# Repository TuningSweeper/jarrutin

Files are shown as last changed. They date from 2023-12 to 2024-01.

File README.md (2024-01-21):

# jarrutin
 Sähköinen jarrutinprojekti
 
 Tästä himmelistä tulee isona sähköinen jarru erääseen muutoin vähemmän sähköiseen järjestelmään.

## Toimintalogiikasta

Jarrutus viimekädessä toimii oikosulkemalla kestomagneettimoottoria.

Moottori on kytketty kolmivaiheiseen diodisiltaan, minkä tarvittaessa oikosulkee n-fetti. Jännitteet ja virrat saattavat olla aika kovia. Sen takia fettiä ajetaan erillisellä ajurilla, mikä pitää huolen siitä, että tilanmuutokset ovat riittävän nopeita. Viimeisimmässä protossa fettejä on neljä rinnan, ettei paketti kuumene liikaa. Seuraavaa iteraatioon pitäisi vähän parantaa diodisillan ja fettien jäähdytystä. Siinä ehjä kannattaa unohtaa piirilevyt ja laittaa reilut rivat, ja niihin komponentit kiinni.

Nopeusanturina on moottorin oma hall-anturi. Sille annetaan 5v ja sieltä tulee avokollektorilähdön kautta nopeustieto. 4N35 -optoerottimella saadaan tehtyä optinen erotus ja samalla jännitteenmuunnos 3.3 V logiikalle. On vähän epäselvää mikä se hall-anturi on, ja toimisiko se kolmella voltilla. Jokatapauksessa optoerotus ei tee pahaa.

Prosessorina on Raspi Zero, mitä voi koodata Arduino IDE:llä. Softalogiikka on yksinkertainen: saapuvien pulssien määrää lasketaan keskeytyksellä. Tässä ohessa on jonkinverran filtteröintiä: a) yksittäiset pulssit vaativat, että signaalin tila ei muutu "pieneen hetkeen", että pulssi lasketaan ja b) pulssista pitää olla kulunut tietty minimiaika, että se lasketaan. Säännöllisin välein (esim. 3hz) tarkastetaan pulssien määrä ja pyöräytetään pulssimäärät sopivan filtterin läpi. Saatua lopputulosta verrataan asetusarvoihin, mikä asettaa PWM-lähdön pulssisuhteen.  Asetusarvoja on kaksi: missä nopeudessa jarru menee päälle ja missä nopeudessa se on täysillä. Tässä välissä voidaan mennä lineaarisesti tai epälineaarisesti. Ohessa on FilttereidenTestauksesta.md, missä on ajatuksia millä noiden filttereiden toimintaa voi opettaa itselleen.

## Ajatuksia

Diodisillalla saadaan myös tarvittaessa tasasuunnattua ja reguloitua muulle elektroniikalle käyttösähkö. Muutaman sadan mikrofaradin elko tulopuolella jaksaa pitää prossun hengissä ehkä noin 100 ms. Tässä pitää huomioida, että tällöin PWM:n suurin pulssisuhde ei voi olla 100%. Systeemissä on kovat jännitteet, mutta kaupasta saanee sopivia regulaattoreita, millä diodillalta saadaan reguloitua 5V sähkö. fi.mouser.com varmasti auttaa asiassa.

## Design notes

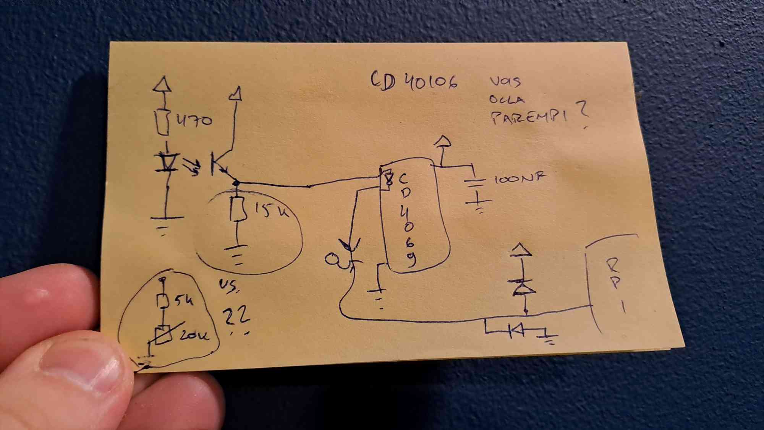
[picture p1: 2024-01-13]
skema-2.jpg

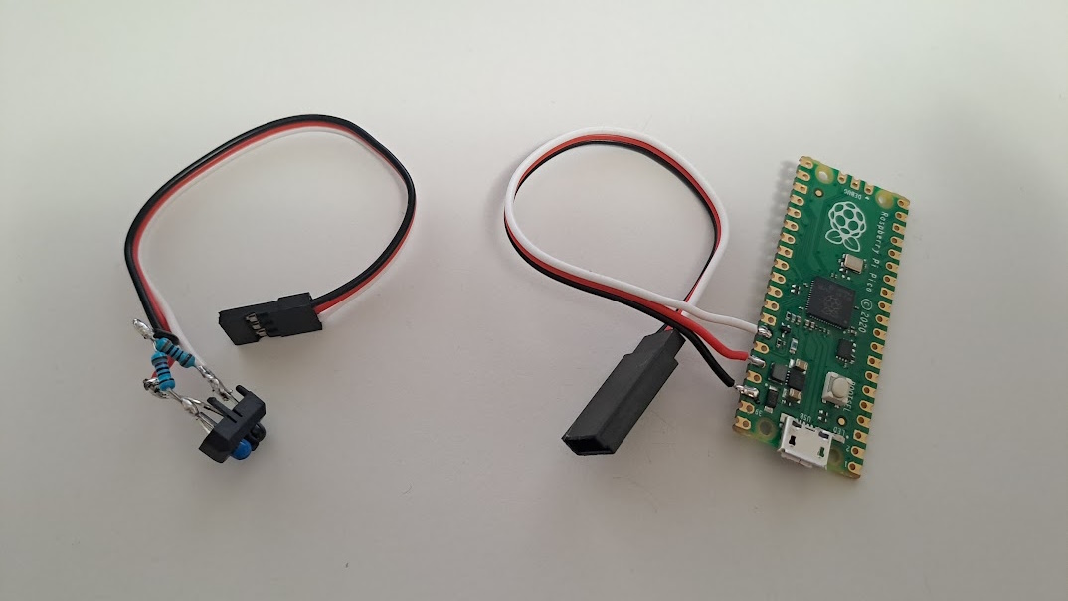
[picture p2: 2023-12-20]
proto-uc-1.jpg

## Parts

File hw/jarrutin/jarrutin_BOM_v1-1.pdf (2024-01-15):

Item Qty Reference(s) | Value | Manufacturer part number | Partco part number | Datasheet | Sourcing
1 | 1 C1 | 4700u | UVZ1H472MRD | UVZ1H472MRD | https://www.nichicon.co.jp/english/series items/catalog pdf/e-uvz.pdf | https://www.partco.fi/fi/elektroniikan-komponentit/passiivit/kondensaattorit/elektrolyyttikondensaattorit/elkot-105c/22643-uvz1h472mrd.html
2 | 1 C2 | 1u | ELKO105 10U 16V | ELKO105 10U 16V | | https://www.partco.fi/fi/elektroniikan-komponentit/passiivit/kondensaattorit/elektrolyyttikondensaattorit/elkot-105c/5890-elko105-10u-16v.html
3 | 3 C3, C4, C5 | 100n | KERKO 100N 50V | KERKO 100N 50V | | https://www.partco.fi/fi/elektroniikan-komponentit/passiivit/kondensaattorit/keraamiset-kondensaattorit/kerkot-500v/16082-kerko-100n-50v.html
4 | 1 SW1 | | | KYT VP22AM VIH | https://www.partco.fi/fi/index.php?controller=attachment&id attachment=3600 | https://www.partco.fi/fi/saehkoemekaniikka/kytkimet/vandal-proof-painokytkimet/26315-kyt-vp22am-vih.html
5 | 1 D1 & Q1 | IR LED & IR FET TCRT5000L | TCRT5000L | https://www.vishay.com/docs/83760/tcrt5000.pdf | https://www.partco.fi/fi/robotit/robottielektroniikkaa/19472-tcrt5000l.html
6 | 6 D2, D3, D4, D5, D6, D7 | MBR1645 | MBR1645 | MBR1645 | https://www.onsemi.com/pdf/datasheet/mbr1635-d.pdf | https://www.partco.fi/fi/elektroniikan-komponentit/aktiivit/diodit/schottky-diodit/2932-mbr1645.html
7 | 3 D8, D9, D10 | D | BAV21 | BAV21 | https://www.vishay.com/docs/85543/bav17.pdf | https://www.partco.fi/fi/elektroniikan-komponentit/aktiivit/diodit/nopeat-diodit/2814-bav21.html
8 | 1 Q2 | IRFIZ34NPdF | IRFIZ34NPdF | IRFIZ34N | https://www.infineon.com/dgdl/Infineon-IRFIZ34N-DataSheet-v01 03-EN.pdf?fileId=5546d462533600a40153562484221fa0 | https://www.partco.fi/fi/elektroniikan-komponentit/aktiivit/transistoritfetit/kytkinfetit-n-kanava/5105-irfiz34n.html
9 | 1 R1 | 10k | 10k trim potentiometer | TRIM MK PYSTY 10K | | https://www.partco.fi/fi/elektroniikan-komponentit/passiivit/trimmerivastukset/monikierrostrimmerit/14209-trim-mk-pysty-10k.html
10 | 2 R2, R5 | 470 | | VASTUS 06W 470R | | https://www.partco.fi/fi/elektroniikan-komponentit/passiivit/vastukset/metallikalvovastukset/normaalit-06w/12483-vastus-06w-470r.html
11 | 1 R3 | 5.6k | | VASTUS 06W 5K6 | | https://www.partco.fi/fi/elektroniikan-komponentit/passiivit/vastukset/metallikalvovastukset/normaalit-06w/12539-vastus-06w-5k6.html
12 | 1 U1 | 40106 | 40106 | 40106B | https://www.ti.com/lit/ds/symlink/cd40106b.pdf | https://www.partco.fi/fi/elektroniikan-komponentit/aktiivit/ttlcmos-logiikkapiirit/logiikkapiirit-40xx/2445-40106b.html
13 | 1 U1 socket | P16 | P16 | P16 | | https://www.partco.fi/fi/elektroniikan-komponentit/aktiivit/piirikannat/2097-p16.html
14 | 1 U2 | TC4420 | TC4420 | | https://ww1.microchip.com/downloads/en/DeviceDoc/21419D.pdf | https://eu.mouser.com/ProductDetail/Microchip-Technology/TC4420EPA?qs=t4j2cOJKO62mJ%2FJS%252BUlxeQ%3D%3D
15 | 1 U2 socket | P8 | P8 | P8 | | https://www.partco.fi/fi/elektroniikan-komponentit/aktiivit/piirikannat/2095-p8.html
16 | 1 U3 | L7805 | L7805 | 7805-DG | https://www.st.com/resource/en/datasheet/l78.pdf | https://www.partco.fi/fi/elektroniikan-komponentit/aktiivit/jaenniteregulaattorit/janniteregulaattorit-78xx/19978-7805-dg.html
17 | 1 U4 | Pico | Raspberry Pico | RASPBERRY PICO | https://datasheets.raspberrypi.com/pico/pico-product-brief.pdf | https://www.partco.fi/fi/raspberry-pi/raspberry-pi-pico/22356-raspberry-pico.html

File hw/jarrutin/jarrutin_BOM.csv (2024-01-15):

Source: | C:\Users\Zokol\dev\jarrutin\hw\jarrutin\jarrutin.kicad_sch
Date: | 15/01/2024 21.27.14
Tool: | Eeschema (6.0.7)
Generator: | C:\Program Files\KiCad\6.0\bin\scripting\plugins/bom_csv_grouped_by_value.py
Component Count: | 24
Individual Components:
Item | Qty | Reference(s) | Value | LibPart | Footprint | Datasheet
 |  | C1 | 100u | Device:C |  | ~
 |  | C2 | 1u | Device:C |  | ~
 |  | C3 | 100n | Device:C |  | ~
 |  | C4 | 100n | Device:C |  | ~
 |  | C5 | 100n | Device:C |  | ~
 |  | D1 | IR LED | LED:IR204A | LED_THT:LED_D3.0mm_IRBlack | http://www.everlight.com/file/ProductFile/IR204-A.pdf
 |  | D2 | 40CPQ100 | Diode:BAV70W | Package_TO_SOT_THT:TO-247-3_Vertical
 |  | D3 | 40CPQ100 | Diode:BAV70W | Package_TO_SOT_THT:TO-247-3_Vertical
 |  | D4 | 40CPQ100 | Diode:BAV70W | Package_TO_SOT_THT:TO-247-3_Vertical
 |  | D5 | 40CPQ100 | Diode:BAV70W | Package_TO_SOT_THT:TO-247-3_Vertical
 |  | D6 | 40CPQ100 | Diode:BAV70W | Package_TO_SOT_THT:TO-247-3_Vertical
 |  | D7 | 40CPQ100 | Diode:BAV70W | Package_TO_SOT_THT:TO-247-3_Vertical
 |  | D8 | D | Device:D |  | ~
 |  | D9 | D | Device:D |  | ~
 |  | D10 | D | Device:D |  | ~
 |  | Q1 | IR FET | Sensor_Optical:BP103BF | LED_THT:LED_D5.0mm_Clear | http://www.b-kainka.de/Daten/Sensor/bp103bf.pdf
 |  | Q2 | IRFIZ34NPdF | Transistor_FET:IRF540N | Package_TO_SOT_THT:TO-220-3_Vertical | http://www.irf.com/product-info/datasheets/data/irf540n.pdf
 |  | R1 | 10k | Device:R_Potentiometer |  | ~
 |  | R2 | 470 | Device:R |  | ~
 |  | R3 | 5k | Device:R |  | ~
 |  | U1 | 40106 | 4xxx:40106 |  | https://assets.nexperia.com/documents/data-sheet/HEF40106B.pdf
 |  | U2 | TC4422 | Driver_FET:TC4422 | Package_DIP:DIP-8-N6_W7.62mm | http://ww1.microchip.com/downloads/en/DeviceDoc/20001420F.pdf
 |  | U3 | L7805 | Regulator_Linear:L7805 |  | http://www.st.com/content/ccc/resource/technical/document/datasheet/41/4f/b3/b0/12/d4/47/88/CD00000444.pdf/files/CD00000444.pdf/jcr:content/translations/en.CD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
 |  | U4 | Pico | MCU_RaspberryPi_and_Boards:Pico | RPi_Pico:RPi_Pico_SMD_TH
Collated Components:
Item | Qty | Reference(s) | Value | LibPart | Footprint | Datasheet
1 | 1 | C1 | 100u | Device:C |  | ~
2 | 1 | C2 | 1u | Device:C |  | ~
3 | 3 | C3, C4, C5 | 100n | Device:C |  | ~
4 | 1 | D1 | IR LED | LED:IR204A | LED_THT:LED_D3.0mm_IRBlack | http://www.everlight.com/file/ProductFile/IR204-A.pdf
5 | 6 | D2, D3, D4, D5, D6, D7 | 40CPQ100 | Diode:BAV70W | Package_TO_SOT_THT:TO-247-3_Vertical
6 | 3 | D8, D9, D10 | D | Device:D |  | ~
7 | 1 | Q1 | IR FET | Sensor_Optical:BP103BF | LED_THT:LED_D5.0mm_Clear | http://www.b-kainka.de/Daten/Sensor/bp103bf.pdf
8 | 1 | Q2 | IRFIZ34NPdF | Transistor_FET:IRF540N | Package_TO_SOT_THT:TO-220-3_Vertical | http://www.irf.com/product-info/datasheets/data/irf540n.pdf
9 | 1 | R1 | 10k | Device:R_Potentiometer |  | ~
10 | 1 | R2 | 470 | Device:R |  | ~
11 | 1 | R3 | 5k | Device:R |  | ~
12 | 1 | U1 | 40106 | 4xxx:40106 |  | https://assets.nexperia.com/documents/data-sheet/HEF40106B.pdf
13 | 1 | U2 | TC4422 | Driver_FET:TC4422 | Package_DIP:DIP-8-N6_W7.62mm | http://ww1.microchip.com/downloads/en/DeviceDoc/20001420F.pdf
14 | 1 | U3 | L7805 | Regulator_Linear:L7805 |  | http://www.st.com/content/ccc/resource/technical/document/datasheet/41/4f/b3/b0/12/d4/47/88/CD00000444.pdf/files/CD00000444.pdf/jcr:content/translations/en.CD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
15 | 1 | U4 | Pico | MCU_RaspberryPi_and_Boards:Pico | RPi_Pico:RPi_Pico_SMD_TH

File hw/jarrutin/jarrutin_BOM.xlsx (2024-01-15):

Item | Qty | Reference(s) | Value | Manufacturer part number | Datasheet | Sourcing
1 | 1 | C1 | 4700u | UVZ1H472MRD | https://www.nichicon.co.jp/english/series_items/catalog_pdf/e-uvz.pdf | https://www.partco.fi/fi/elektroniikan-komponentit/passiivit/kondensaattorit/elektrolyyttikondensaattorit/elkot-105c/22643-uvz1h472mrd.html
2 | 1 | C2 | 1u | ELKO105 10U 16V |  | https://www.partco.fi/fi/elektroniikan-komponentit/passiivit/kondensaattorit/elektrolyyttikondensaattorit/elkot-105c/5890-elko105-10u-16v.html
3 | 3 | C3, C4, C5 | 100n | KERKO 100N 50V |  | https://www.partco.fi/fi/elektroniikan-komponentit/passiivit/kondensaattorit/keraamiset-kondensaattorit/kerkot-500v/16082-kerko-100n-50v.html
 | 1 | SW1 |  |  | https://www.partco.fi/fi/index.php?controller=attachment&id_attachment=3600 | https://www.partco.fi/fi/saehkoemekaniikka/kytkimet/vandal-proof-painokytkimet/26315-kyt-vp22am-vih.html
4 | 1 | D1 & Q1 | IR LED & IR FET | TCRT5000L | https://www.vishay.com/docs/83760/tcrt5000.pdf | https://www.partco.fi/fi/robotit/robottielektroniikkaa/19472-tcrt5000l.html
5 | 6 | D2, D3, D4, D5, D6, D7 | 40CPQ100 | 40CPQ100 | https://www.irf.com/product-info/datasheets/data/40cpq080.pdf | https://www.partco.fi/fi/elektroniikan-komponentit/aktiivit/diodit/schottky-diodit/2941-40cpq100.html
6 | 3 | D8, D9, D10 | D | BAV21 | https://www.vishay.com/docs/85543/bav17.pdf | https://www.partco.fi/fi/elektroniikan-komponentit/aktiivit/diodit/nopeat-diodit/2814-bav21.html
7 | 1 | Q2 | IRFIZ34NPdF | IRFIZ34NPdF | https://www.infineon.com/dgdl/Infineon-IRFIZ34N-DataSheet-v01_03-EN.pdf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 | https://www.partco.fi/fi/elektroniikan-komponentit/aktiivit/transistoritfetit/kytkinfetit-n-kanava/5105-irfiz34n.html
8 | 1 | R1 | 10k | 10k trim potentiometer |  | https://www.partco.fi/fi/elektroniikan-komponentit/passiivit/trimmerivastukset/monikierrostrimmerit/14209-trim-mk-pysty-10k.html
9 | 2 | R2, R5 | 470 |  |  | https://www.partco.fi/fi/elektroniikan-komponentit/passiivit/vastukset/metallikalvovastukset/normaalit-06w/12483-vastus-06w-470r.html
10 | 1 | R3 | 5.6k |  |  | https://www.partco.fi/fi/elektroniikan-komponentit/passiivit/vastukset/metallikalvovastukset/normaalit-06w/12539-vastus-06w-5k6.html
11 | 1 | U1 | 40106 | 40106 | https://www.ti.com/lit/ds/symlink/cd40106b.pdf | https://www.partco.fi/fi/elektroniikan-komponentit/aktiivit/ttlcmos-logiikkapiirit/logiikkapiirit-40xx/2445-40106b.html
 | 1 | U1 socket | P16 | P16 |  | https://www.partco.fi/fi/elektroniikan-komponentit/aktiivit/piirikannat/2097-p16.html
12 | 1 | U2 | TC4420 | TC4420 | https://ww1.microchip.com/downloads/en/DeviceDoc/21419D.pdf | https://eu.mouser.com/ProductDetail/Microchip-Technology/TC4420EPA?qs=t4j2cOJKO62mJ%2FJS%252BUlxeQ%3D%3D
 | 1 | U2 socket | P8 | P8 |  | https://www.partco.fi/fi/elektroniikan-komponentit/aktiivit/piirikannat/2095-p8.html
13 | 1 | U3 | L7805 | L7805 | https://www.st.com/resource/en/datasheet/l78.pdf | https://www.partco.fi/fi/elektroniikan-komponentit/aktiivit/jaenniteregulaattorit/janniteregulaattorit-78xx/19978-7805-dg.html
14 | 1 | U4 | Pico | Raspberry Pico

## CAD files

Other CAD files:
hw/jarrutin/KiCad-RP-Pico-main/SketchUp Model/Pico.skp

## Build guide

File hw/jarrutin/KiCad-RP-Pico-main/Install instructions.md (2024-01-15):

# Install instructions

## 1. Copy the files locally

Copy the `RP-Pico Libraries` folder wherever you like on your computer.

## 2. Install the Raspberry Pi Pico board schema symbol

Use the `KiCad | Preferences | Manage Symbol Libraries...` command to manage the symbol library:

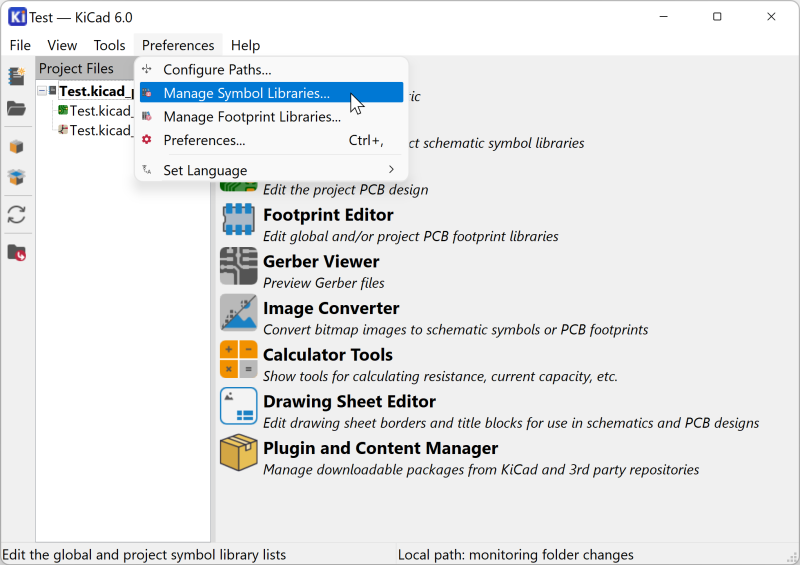
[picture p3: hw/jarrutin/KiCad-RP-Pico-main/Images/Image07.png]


then select the global tab and click on the folder button:

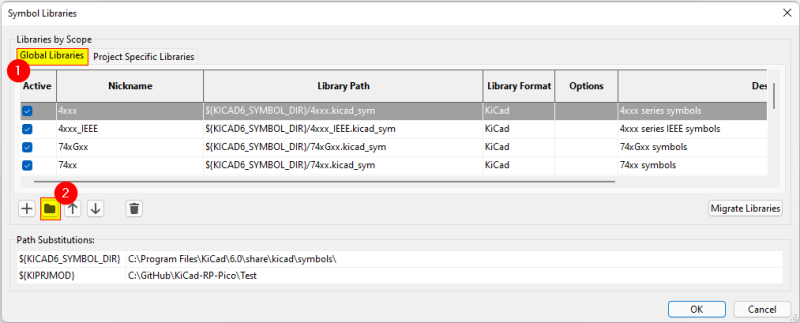
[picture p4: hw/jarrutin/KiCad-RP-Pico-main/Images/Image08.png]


navigate to the `RP-Pico Libraries` folder, select the `MCU_RaspberryPi_and_Boards.kicad_sym` file and open it:

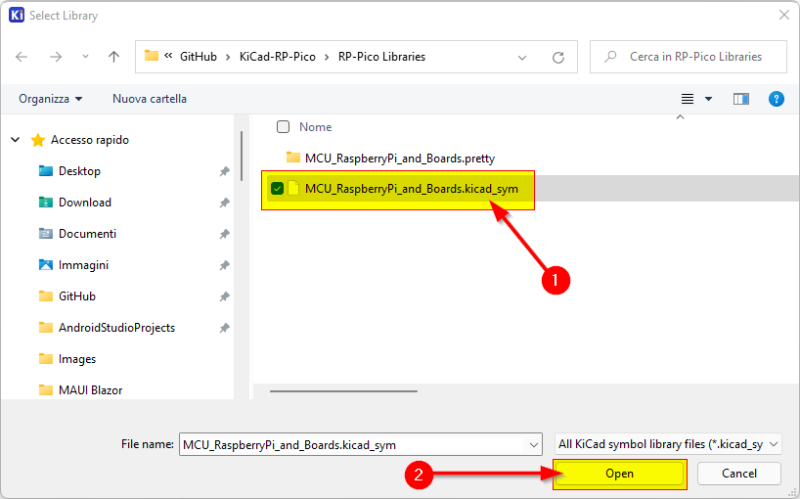
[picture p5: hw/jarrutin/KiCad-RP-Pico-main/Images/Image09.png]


et voilà, the first step is completed:

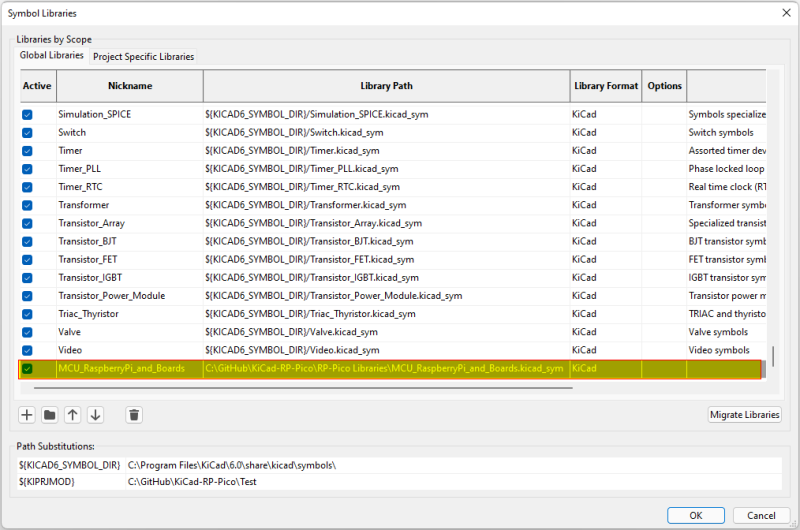
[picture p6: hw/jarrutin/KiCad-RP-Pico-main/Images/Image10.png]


You can now close the symbol libraries manager window.

## 3. Install the Raspberry Pi Pico board footprint

You can use a similar approach to add the footprint to the footprint libraries manager, but I've found some issues that I've solved using the footprint editor, so here are the steps I suggest you to follow:

Open the footprint editor

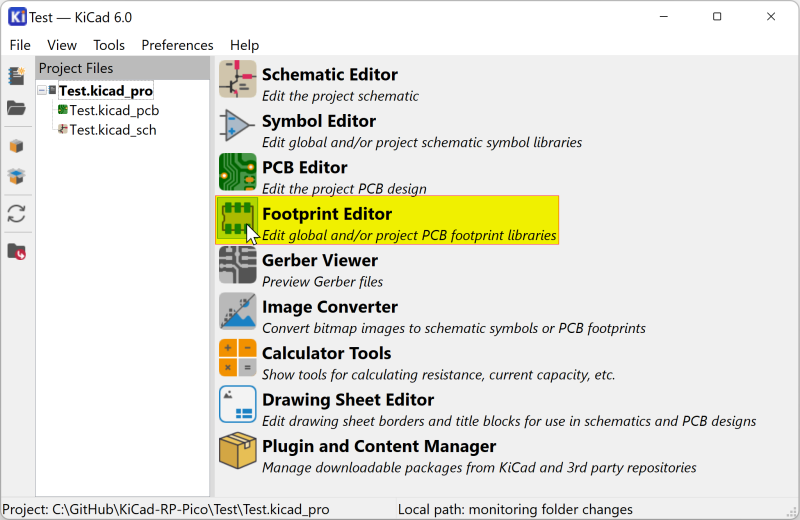
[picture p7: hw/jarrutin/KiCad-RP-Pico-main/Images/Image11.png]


wait for the footprints to load... then use the `File | Add Library` command:

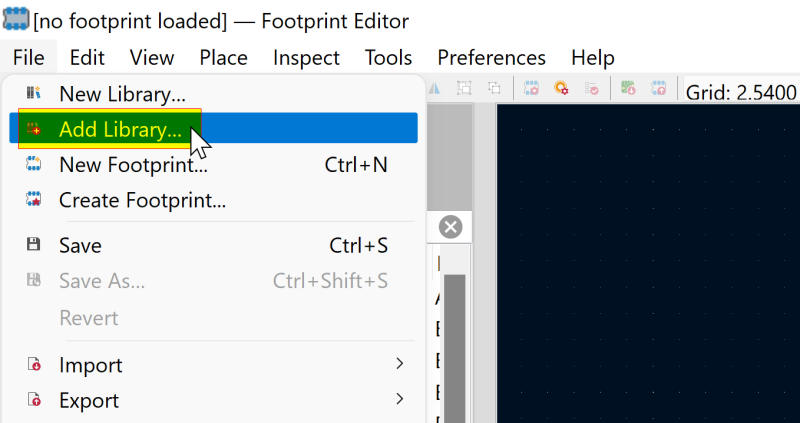
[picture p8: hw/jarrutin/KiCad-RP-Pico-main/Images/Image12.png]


confirm the `Global` choice:

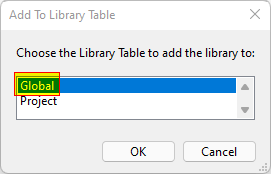
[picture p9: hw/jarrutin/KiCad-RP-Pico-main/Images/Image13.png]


and select the `MCU_RaspberriPi_and_Boards.pretty` folder (yes, the folder represent a footprint library on KiCad):

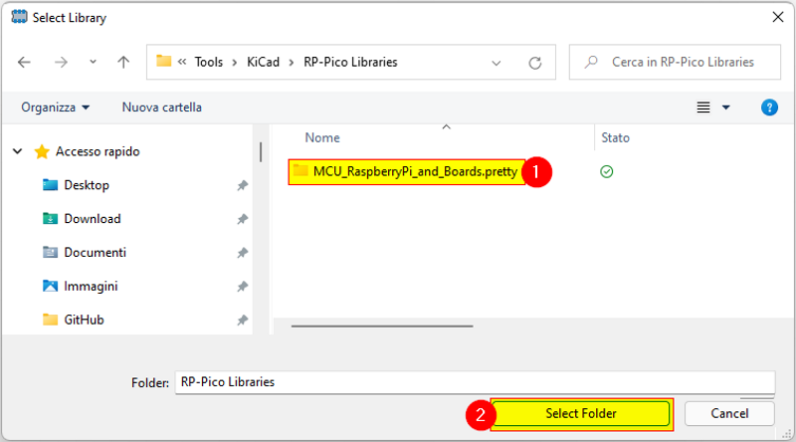
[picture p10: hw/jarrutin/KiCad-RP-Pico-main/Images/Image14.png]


Now the library is installed on KiCad with the Raspberry Pi Pico footprint (double click on it to see it on the editor pane):

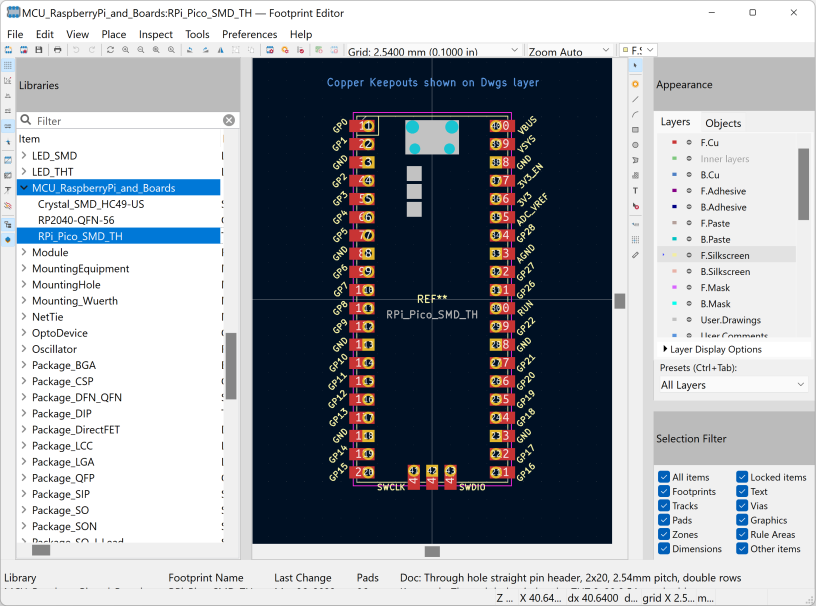
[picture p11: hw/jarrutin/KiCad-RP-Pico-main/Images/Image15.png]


Don't close the windows as the next step start from here.

## 4. Install the Raspberry Pi Pico board footprint 3D visual

If not already open, open the the footprint editor

symbol library manager

double click on the `RPi_Pico_SMD_TH` footprint from the `MCU_RaspberriPi_and_Boards` library and then click on the `Footprint properties` icon:

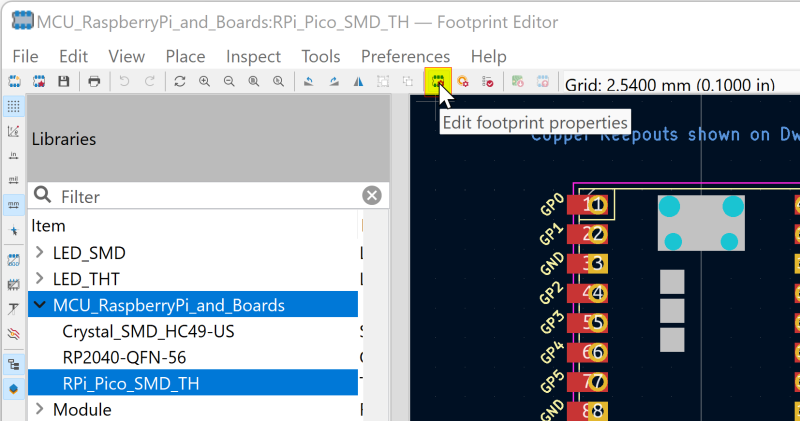
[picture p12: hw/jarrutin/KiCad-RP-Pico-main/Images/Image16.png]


In the footprint properties window, first select the `3D Settings` tab. Please note that the preview shows only the PCB board with the footprint added on step 3, without any 3D representation of the Raspberry Pi Pico board. Now click on the folder icon to add the 3D model:

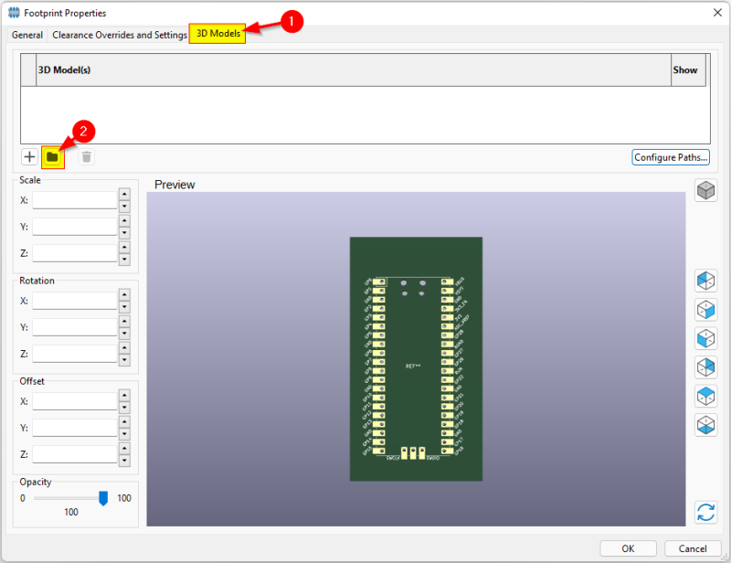
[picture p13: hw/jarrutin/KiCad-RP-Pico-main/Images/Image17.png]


Navigate to the `RP-Pico Libraries` folder, select the `Pico.wrl` file and wait until the model is shown in the right panel, then confirm with OK:

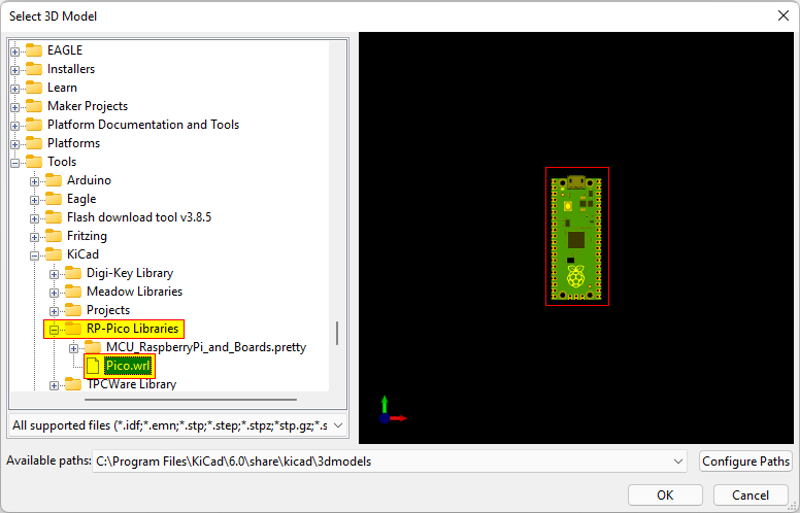
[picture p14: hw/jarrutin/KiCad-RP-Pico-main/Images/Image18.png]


The model is already scaled and translated to match the footprint:

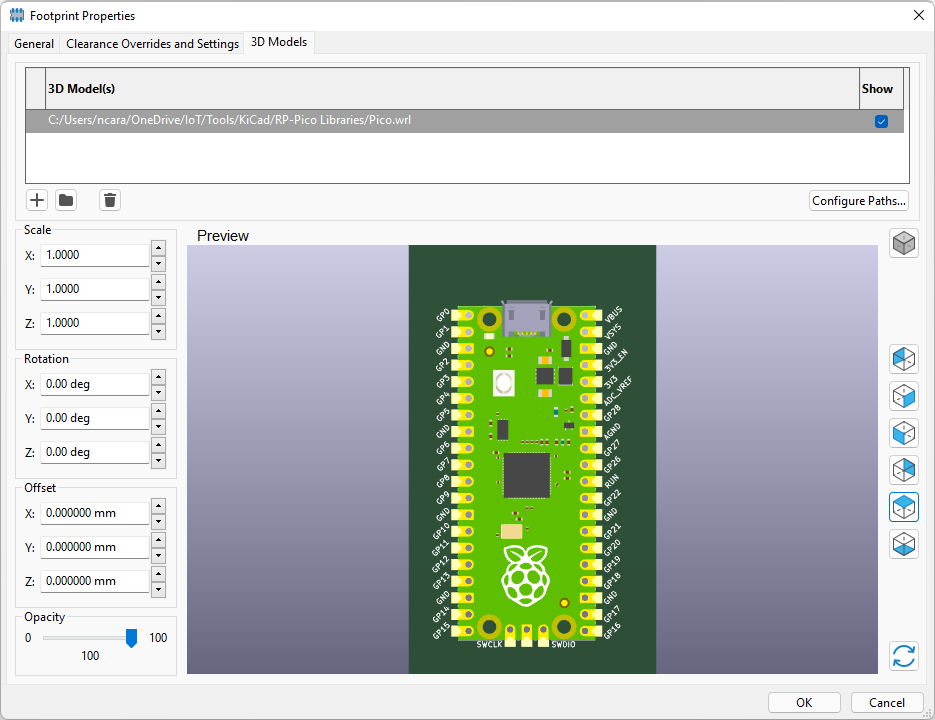
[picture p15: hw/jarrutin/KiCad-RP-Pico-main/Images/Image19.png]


now close the `Footprint Properties` window, and the `Footprint Editor`, obviously saving the changes.

## Conclusion

Now that you've installed the schema and footprint and added the 3D model to the footprint, you can use the Raspberry Pi Pico board on your KiCad projects.

I've also added a test KiCad Project on the `Test` folder, that you can use to see an example of it.

Have fun!

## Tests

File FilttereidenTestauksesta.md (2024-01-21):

# Filtteriden tuunauksesta

Systeemissä on pari jännempää filtteriä: on eksponentiaalinen liukuva keskiarvo ja sitten on epälinaarisuutta tuomassa potenssifunktio. Näitä voi testata ja ihmetellä kaikkein helpoiten erilaisilla www-pohjaisilla c-kääntäjillä.

Esim. sivustoon https://www.onlinegdb.com/online_c_compiler voi pasteta c-koodin ja painaa run, minkä jälkeen näkee mitä koodi tekee. Tuolle voi siis tarjota seuraavia testipalikoita. Se toivottavasti auttaa ymmärtämään miten ne toimii.

## Eksponentiaalinen liukuva keskiarvo

```
#include <stdio.h>

#define INPUT_FILTER_N 6
#define INPUT_FILTER_ALPHA 0.4

unsigned int inputBuffer[INPUT_FILTER_N];

unsigned int getFilteredInputValue(unsigned int value) {
	// siirrä arvoja yksi pykälä eteenpäin
	for(int i=INPUT_FILTER_N-1; i>0; i--) {
		inputBuffer[i] = inputBuffer[i-1];
	}
	// ja laita uusin arvo indeksiin 0
	inputBuffer[0] = value;
	
	// ja filtteröi. Tässä siis lasketaan tietyllä tavalla painotettu summa puskurin arvoista
	// ja siitä sitten 
	float filteredValue = inputBuffer[0];
	for (int i=INPUT_FILTER_N; i>0; i--) {
		filteredValue = (INPUT_FILTER_ALPHA * inputBuffer[i]) + ((1.0 - INPUT_FILTER_ALPHA) * filteredValue);
	}

	// palautetaan se kokonaislukuna
	return (unsigned int) filteredValue;
}

int main() {
    int val[20] = {0,0,0,0,0,0,10,10,10,10,20,10,10,10,10,10,10,10,10,10,10};
    // Write C code here
    for(int i=0; i<20; i++) {
        printf("in: %i   out: %i\n", val[i], getFilteredInputValue(val[i]));
    }
    return 0;
}
```

## Epälineaarisuutta tuova potenssifunktio
Funktion käppyrää voi tarkastella ja eksponenttiä tuunailla esim. URLissa:
https://www.wolframalpha.com/input?i=plot+y%3D255*%28x%2F255%29%5E0.25+from+0+to+255

```
#include <stdio.h>
#include <math.h>

double powerScaling(int input, double exponent) {
    double result;
    
    result = 255 * pow((double) input / 255, exponent);
    if (result < 0) result = 0;
    if (result > 255) result = 255;

    return result;
}

int main() {
    double exponent = 0.25;
    double result;

    for (int i = 0; i<256; i=i+1) {
        result = powerScaling(i, exponent);
        printf("input %i  \t   power scaling output: %i\n", i, (int) result);
    }

    return 0;
}
```

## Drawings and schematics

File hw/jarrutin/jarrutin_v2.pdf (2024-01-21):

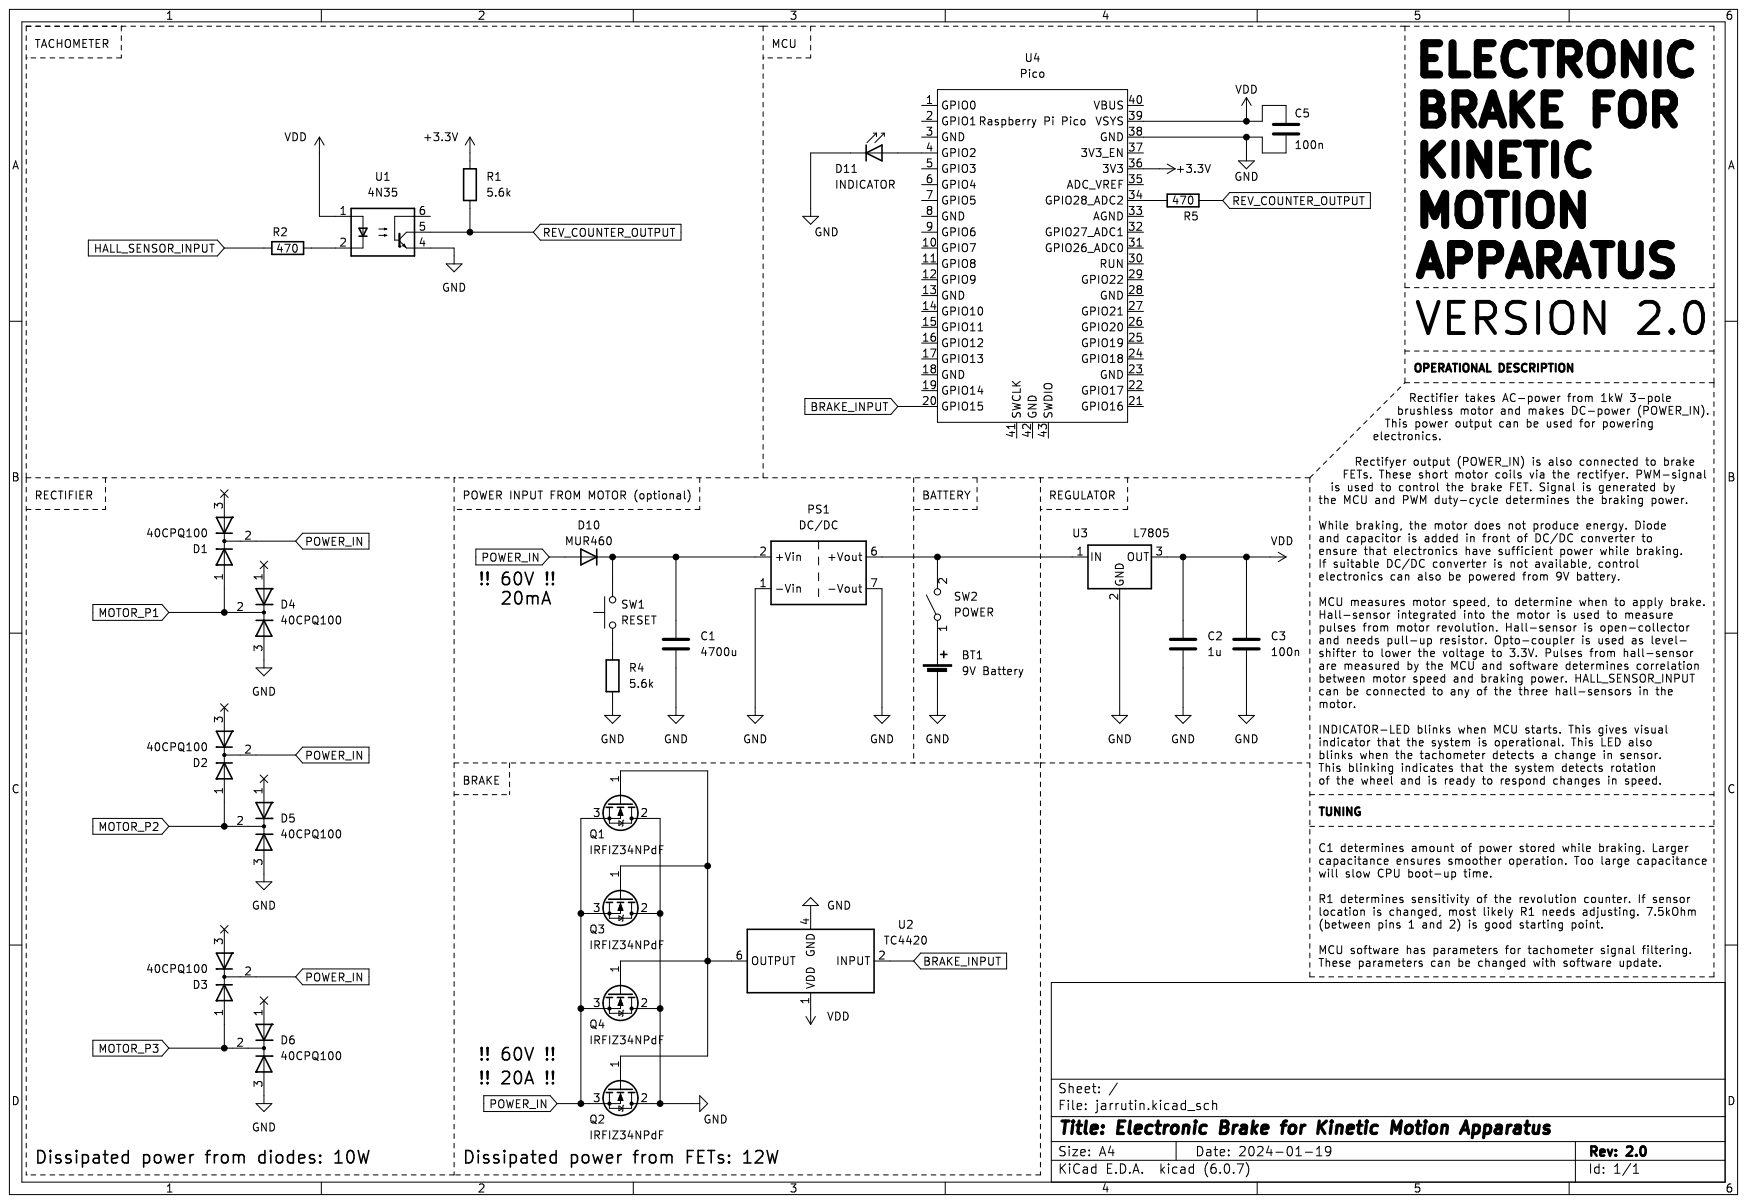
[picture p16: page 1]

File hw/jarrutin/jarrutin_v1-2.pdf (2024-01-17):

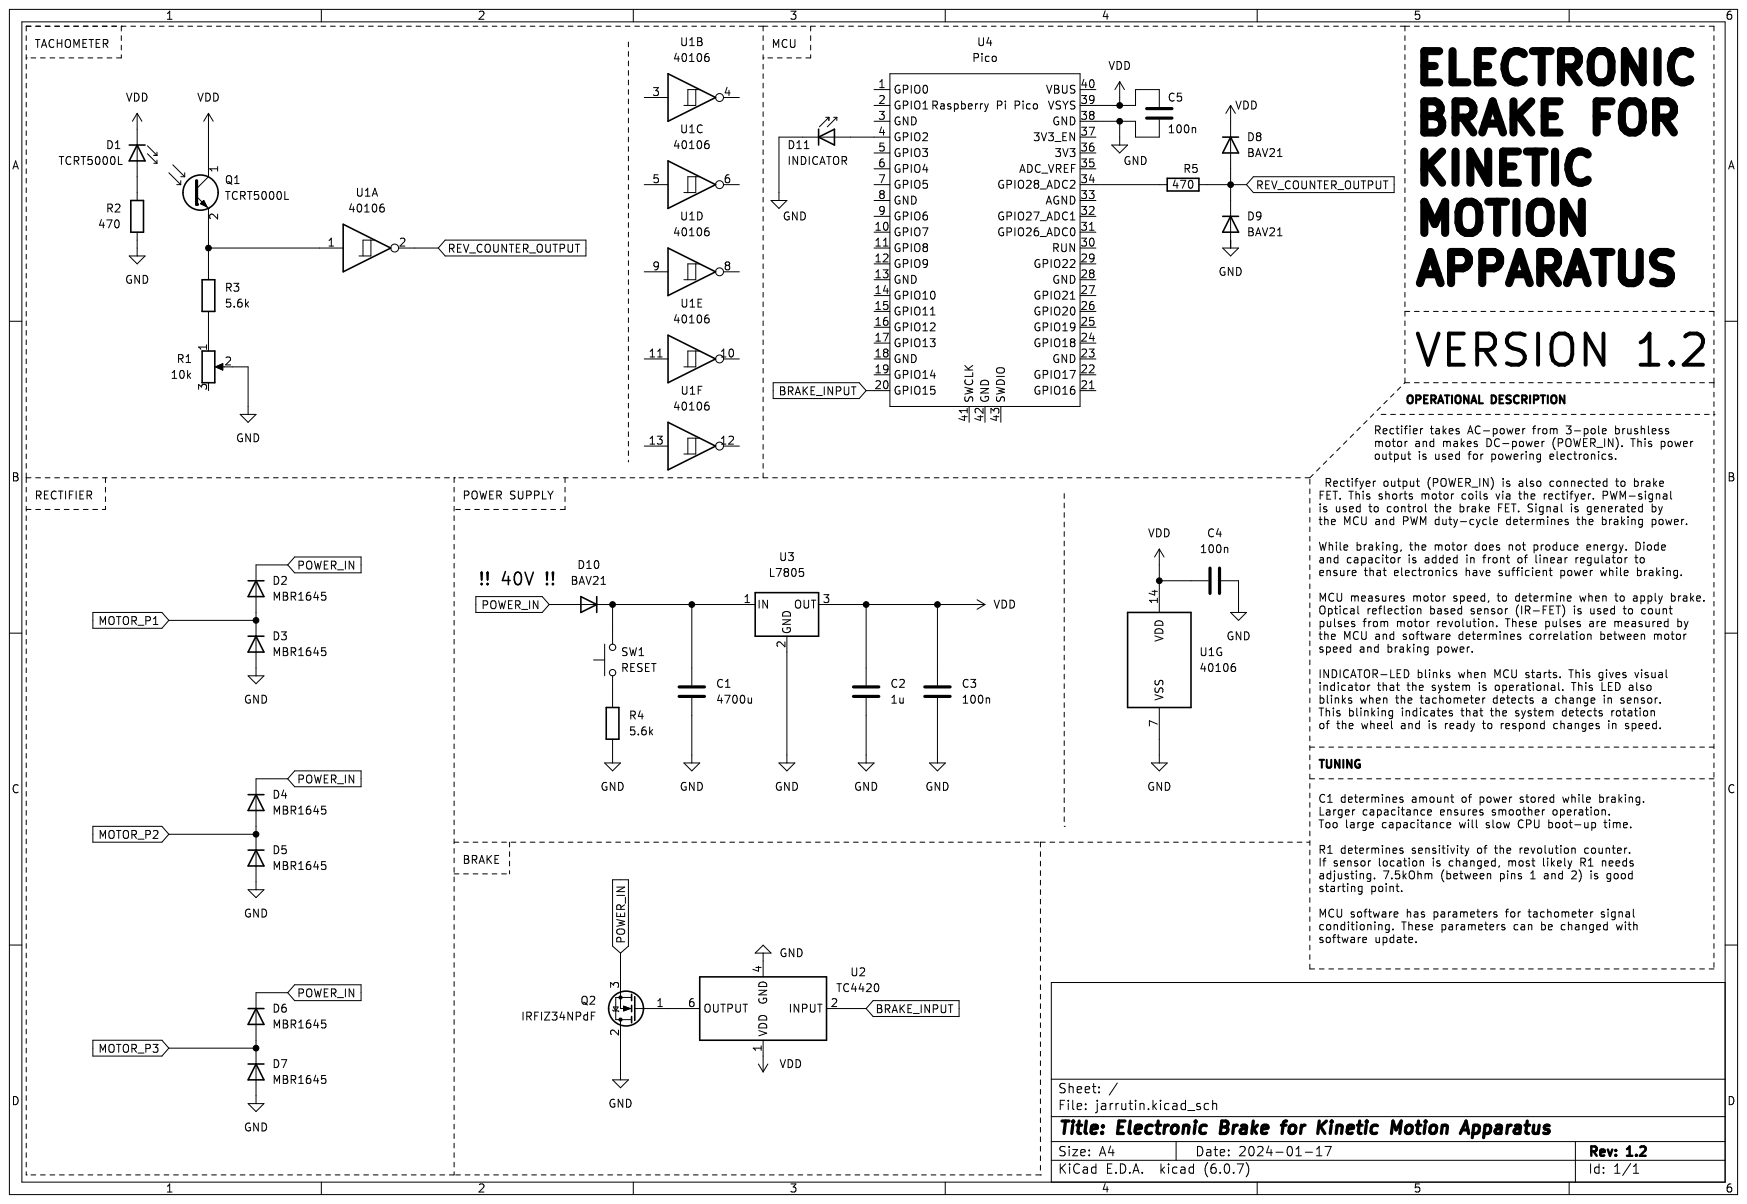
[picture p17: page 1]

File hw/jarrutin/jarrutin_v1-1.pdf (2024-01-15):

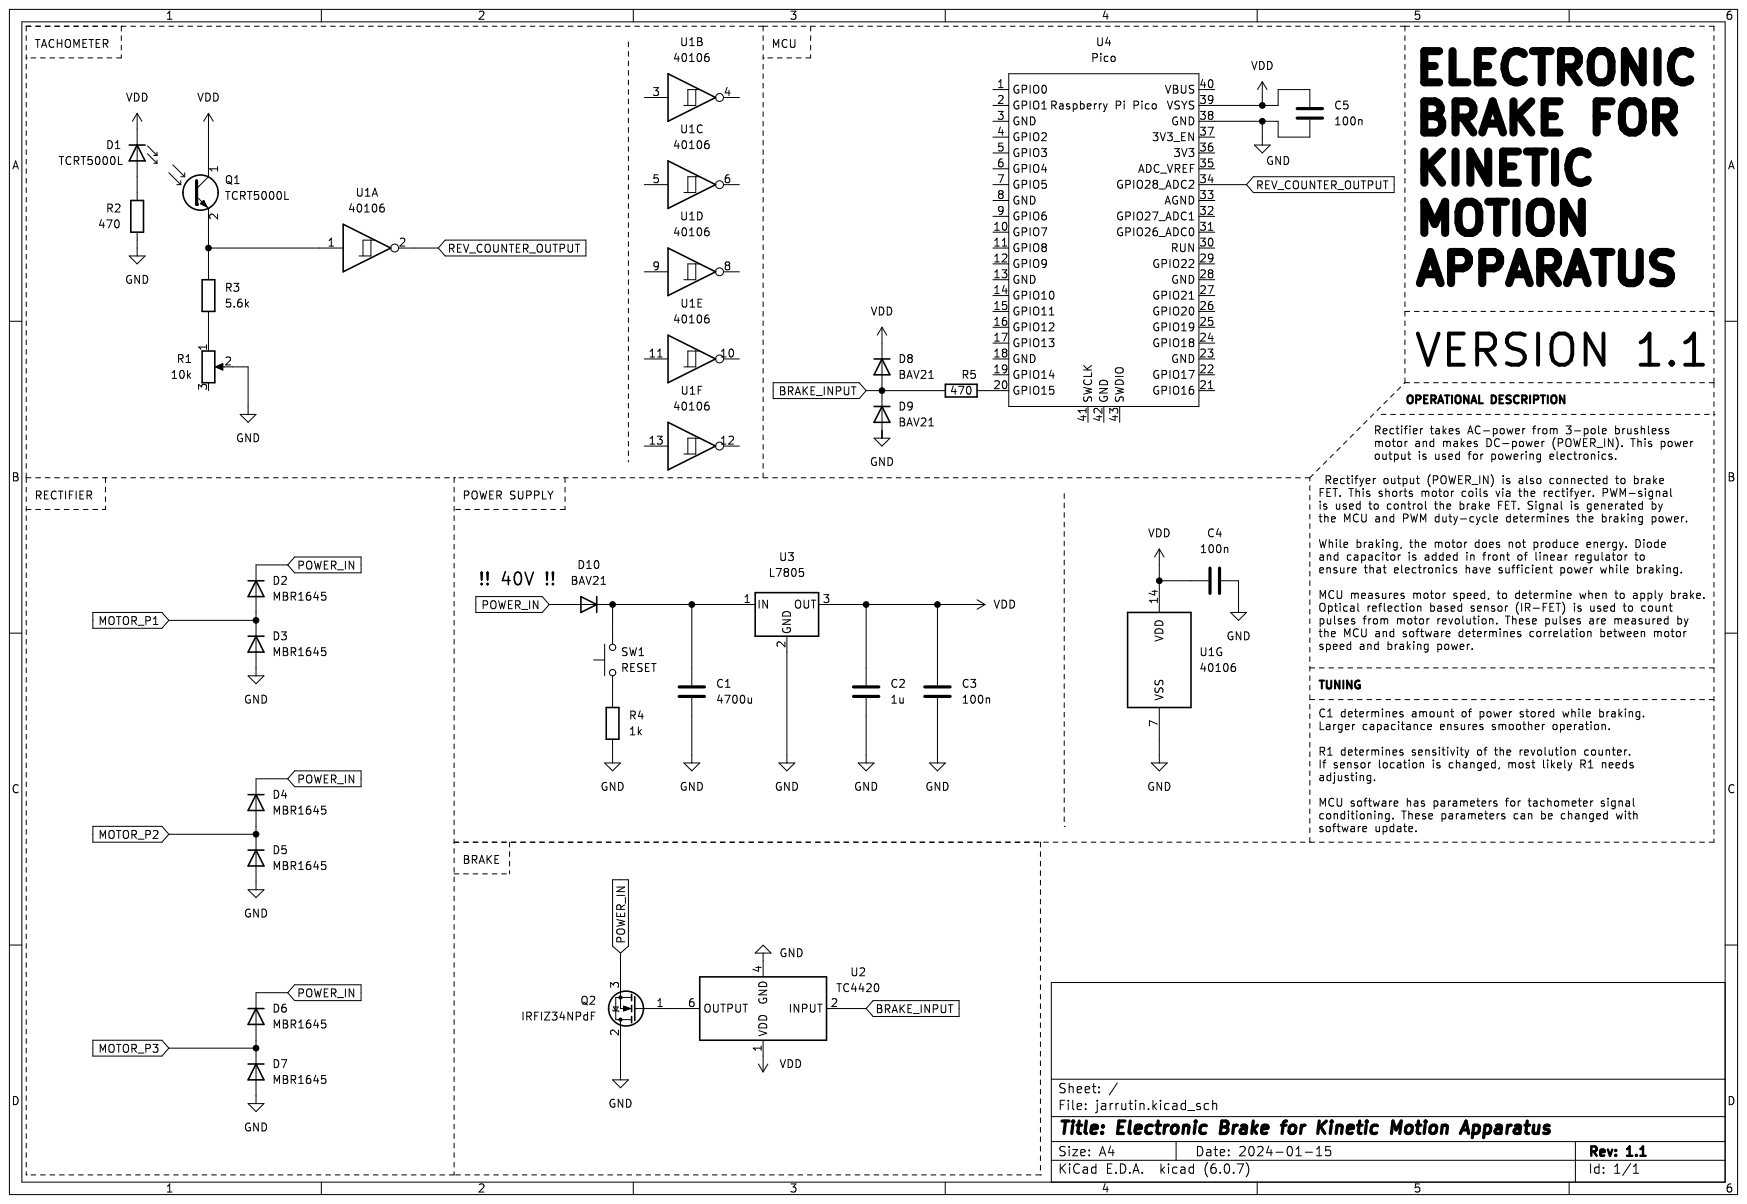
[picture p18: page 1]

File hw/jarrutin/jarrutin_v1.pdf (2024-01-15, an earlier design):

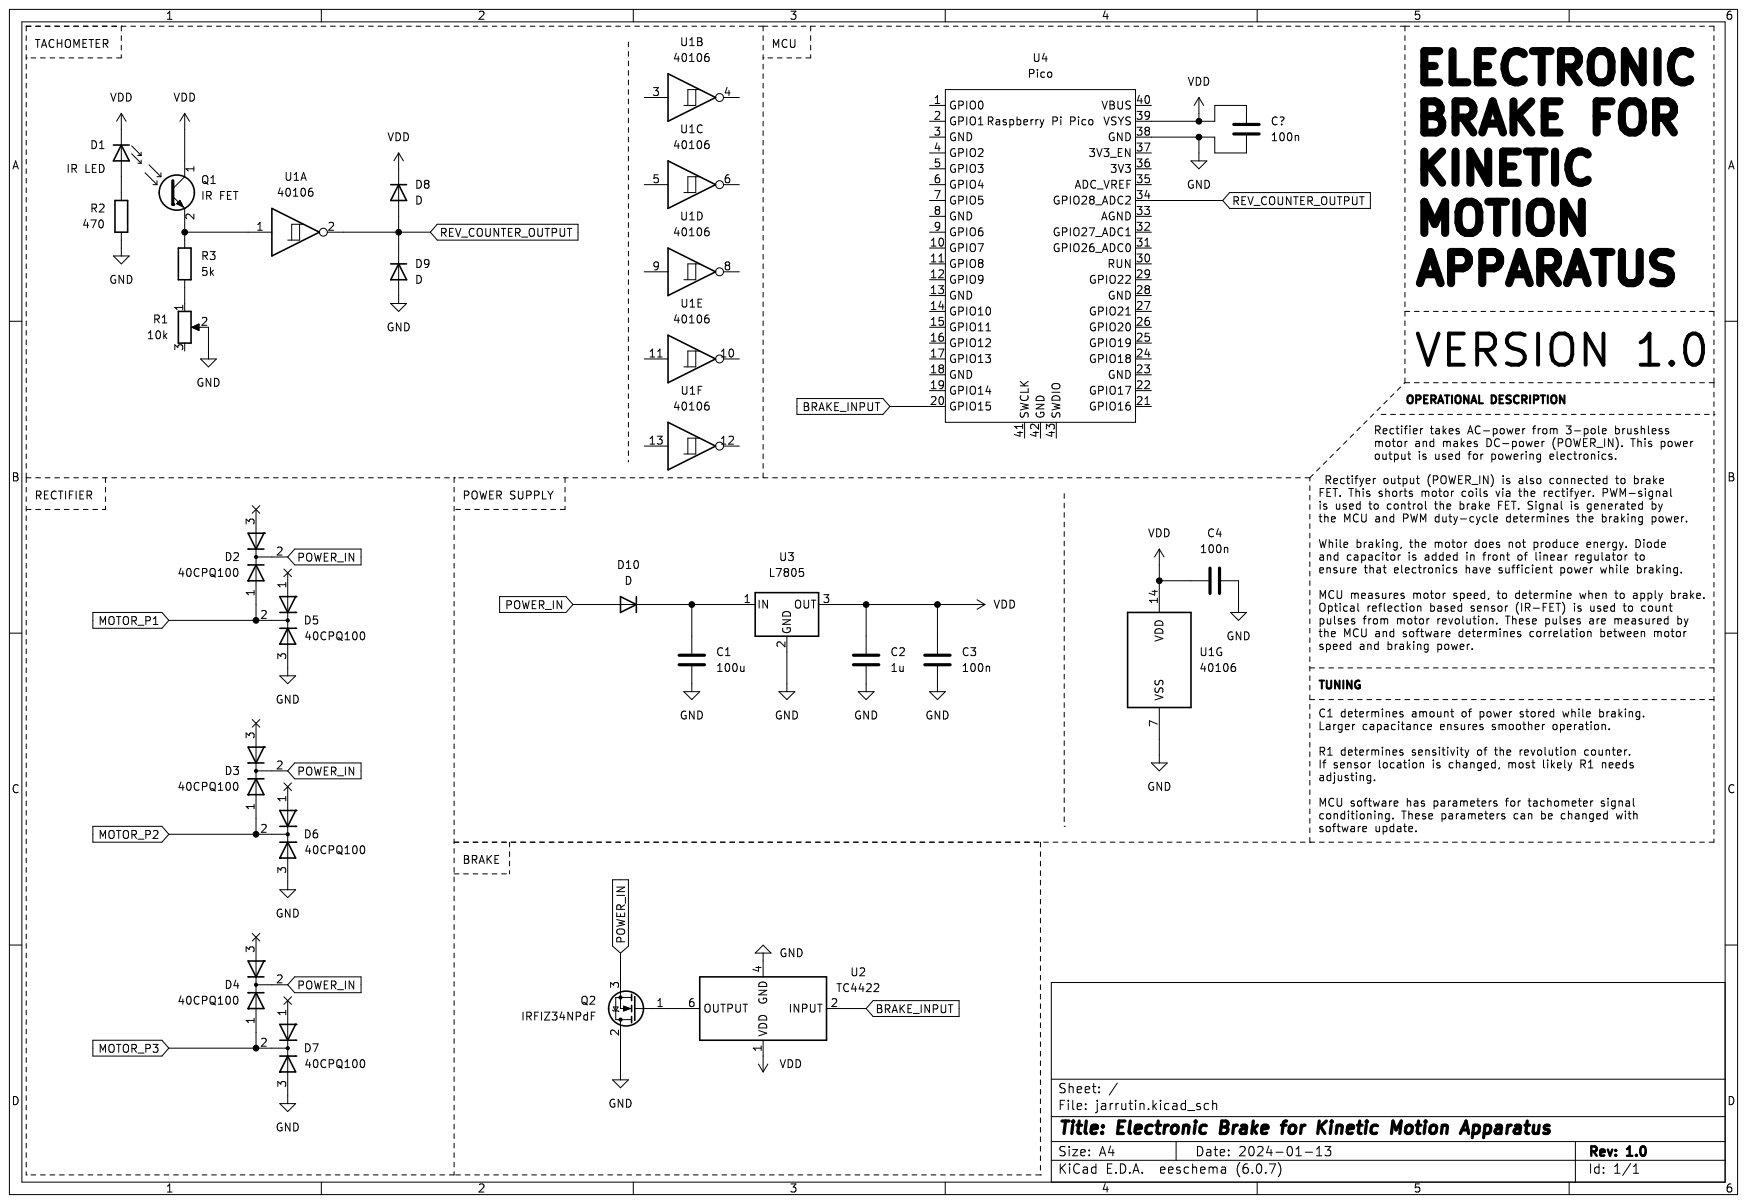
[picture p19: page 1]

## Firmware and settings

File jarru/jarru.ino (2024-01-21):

/* 
	Jarru
	
	Yritetty kirjoittaa niin, että on luettavissa ja ymmärrettävissä.
	Ei siis mitään turhan hienoja juttuja tai mitään kirjastoja.

	Arduino IDE: 2.2.1
	Board manager url: https://github.com/earlephilhower/arduino-pico/releases/download/global/package_rp2040_index.json
	Board: Raspberry Pi Pico
	´

changelog

	ver 0.1:
		Eka proto Arduinolla (joku ATMEGA)
		Periaate todettiin toimivaksi
		
	ver 0.2:
		Porttaus Raspberry Pi Picolle
		Kommentoitu
		Parametrit nätisti
		Lisätty suodin vähän pehmentämään jarrutuksen muuttumista

	ver 0.3:
		Kovaa taistelua: tabs vs spaces
		Lisätty sensorled

	ver 0.4:
		tabs vs spaces erä II.
		Viety PWM-lähtö takanurkkaan
		Anturituloon ylösvetovastus, ettei kellu.
		Askarreltu kohinasuodinta tuloon

	ver 0.5:
		tabs vs spaces erä III.
		askarreltu uusi status led
		test-moodi jarrun voimakkuudelle
		test-moodi anturin asemoinnille
		parametrisoitu input-kohina-filtteri
		uusi output filtteri

	ver 0.6:
		säädetty parametrejä. Tuntu jo ihan hyvältä

	ver 0.7:
		lisätty epälineaarisuus-optio. Paperilla se vaikuttaa hyvältä. EI OLE TESTATTU!
		Tuunattu parametrejä. Veikkaus on, että nyt on aika hyvä.
		Korjattu eksponentiaalisen liukuvan keskiarvon suotimen bugi
		Lisätty vähän kommentteja.
*/

// ****************
// Toimintamoodista

// Tää moodi on vain jarrutusvoiman testaukseen. Jos määritelty, niin tää
// asettaa jarruvoiman asteikolla 0..255 tiettyyn tasoon eikä tee *mitään muuta*
// Huom. jos laite ottaa oman virtansa moottorilta, niin jarruvoimalla 255
// (tai lähellä sitä) energiaa ei välttämätä riitä cpu:lle ja se kaatuu
//#define TESTMODE_BRAKELEVEL 250

// Tää moodi on vain anturin asemoinnin testaukseen. Jos määritelty, niin tää
// replikoi anturin tilaa, eikä tee *mitään muuta*. Eli vilkkuu kun pyörii.
//#define TESTMODE_LEDBLINKER

// jos tää on määritelty, niin tää vilkuttelee sitä levyllä olevaa lediä anturin tahdissa.
// Huom. tän vilkku on *puolet* hitaampaa kuin mitä anturi näkee. Tuotantoa varten pois päältä?
// Vie kuitenkin virtaa turhaan..
#define SENSORLED

// jos tämä on määritelty, tulosteleee USB-uarttiin miten menee.
// tuotantoversiota varten kommentoi pois.
// #define SERIALDEBUG


// ************************
// käytön asetuksia

// BRAKE_LEVEL_MIN kertoo millä nopeudella (pulssia/sekunti) jarrutus alkaa
//#define BRAKE_LEVEL_MIN 20
#define BRAKE_LEVEL_MIN 15

// BRAKE_LEVEL_MAX kertoo millä nopeudella (pulssia/sekunti) jarrutus on TÄYSILLÄ
//#define BRAKE_LEVEL_MAX 45
#define BRAKE_LEVEL_MAX 30

// LOOP_INTERVAL (ms) kertoo kuinka usein tila päivitty. 333 ms, eli 3hz lienee aika sopiva.
// Mitä tiheämmin systeemin tilaa päivitetään, sitä epätarkempi on nopeuden mittaus nykymallissa.
// Ja muutenkin: koska systeemissä on aika suuri liikemäärä, ei asioita tarvitse päivittää kovin
// ripeästi. Hihasta vedettynä 250 ms (eli 4hz) ... 500 ms (2 hz) kuulostaa sopivalta väliltä.
#define LOOP_INTERVAL 333


// **************************************
// optisen anturin kohinanpoistoa varten

// INPUT_PULSE_HOLDOFF (ms) kertoo kuinka pitkä aika kahden pulssin välillä pitää vähintään olla, että
// se lasketaan. Tämä samalla rajaa systeemin laskeman maksiminopeuden.
// esim. 10 ms = 100 pulssia sekunti. Jos kierros on 48 pulssia, niin se tarkoittaa 120 rpm.
// Arvolla 0 tämä optio on pois päältä.
#define INPUT_PULSE_HOLDOFF 0

// Nämä kaksi kertoo, että kuinka monta kertaa tulosignaalin tila mitataan keskeytyksen liipaisun jälkeen
// ja kuinka monta näistä pitää olla samoja, että se pulssi lasketaan. Tämä siis suodattaa pois tosi nopeat piikit.
// arvoilla 0 tämä feature on pois päältä.  Sen voi antaa olla jotain, niin eipähän pienet häiriöpiikit häiritse
// (vaikka ei niitä hall-anturn kohdalla varmaan nähdäkään)
#define INPUT_PULSE_RECHECKS 2
#define INPUT_PULSE_RECHECK_MIN 2



// **********************************************
// Raudan kytkennät ja pinnit ja siihen liittyvät

// nää määrittelis minne PWM ja sensori ja ledi olis kytketty.
#define PWM_OUTPUT_PIN 15
#define SENSOR_INPUT_PIN 28
#define LED_PIN 2

// PWM_FREQUENCY kertoo millä taajuudella fettiä ajetaan. korkeampi taajuus vie vinkumisen korkeille taajuuksille
// Korkeat taajuudet ei kuulu, mutta fetti voi lämmetä enemmän. Vois olla kiinnostavaa myös kokeilla
// pieniä arvoja miltä se *tuntuu* ja kuulostaa (100? en tiedä?).
#define PWM_FREQUENCY 2000

// PWM_MAX kertoo pwm-jarrun suurimman arvon välillä 0..255.
// JOS sen jarrun toimintasähkö otetaan moottorista, pitää tähän jättää vähän löysää, että prossun virtaa
// ei oteta kokonaan pois 100% pwm:llä. (255 arvo johtaa prossun boottaamiseen.)
// arvolla 251 noin 1% moottorin tuottamasta energiasta on jarruohjaimen käytettävissä.
#define PWM_MAX 255


// ***********************************************
// Filtterioptiot ja muut pehmentimet.

// USE_OUTPUT_FILTER kertoo käytetäänkö PWM-lähdön pehmentämiseen filtteriä vai ei.
// Kommentoi pois jos ei. Filtterin tyyppi on tavallinen liukuva keskiarvo.
#define USE_OUTPUT_FILTER
// Output filter on ihan vaan liukuva keskiarvo tietyllä N:llä. Jos LOOP_INTERVAL on 333 ja N on 6
// tarkoittaa se, sitä, että mutokset jarruvoimassa tulevat voimaan täysimääräisinä kahdessa sekunnissa.
#define OUTPUT_FILTER_N 6

// USE_INPUT_FILTER pehmentää myös jarruvoimaa, mutta tämä pehmentää anturilta tulevia lukemia.
//#define USE_INPUT_FILTER
// Filtteri on eksponentiaalinen liukuva keskiarvo, eli viimeisintä arvoa painotetaan eniten ja vanhinta vähiten
// INPUT_FILTER_N kertoo suotimen pisteiden määrän.  333 ms loopIntervallilla n=6 tarkoittaa kahta sekuntia
#define INPUT_FILTER_N 6
// INPUT_FILTER_ALPHA on ulostulon suotimen painotusten "jyrkkyys". Suurempi arvo painottaa tuoreita
// arvoja paljon enemmän. Arvolla 0 ei oikeastaan enää tehdä mitään filtteröintiä. 
#define INPUT_FILTER_ALPHA 0.4


// ********************************************************************
// Epälinearisointi

// Käytetäänkö jarrutustason asetuksessa epälineaarista funktiota?
// vaihtoehtoisinen optio on toistaiseksi POWER. ehkä joskus tulee toinenkin optio
// jos tämä on kommentoitu pois, niin PWM:n arvot ovat lineaariset.
#define NONLINEARIZATION_FUNCTION POWER

// Määrittää POWER -funktion eksponentin. Vaikuttaa sen "jyrkkyyteen". Pienempi on "jyrkempi"
// Kyseessä on yksinkertainen potenssifunktio. Millään tavalla järkeviä eksponentin arvoja
// on luvut välillä 0.1 .. 0.8.  joku 0.25 on ehkä hyvä aloituspiste.
// Funktion käppyrää voi tarkastella ja eksponenttiä tuunailla esim. URLissa:
// https://www.wolframalpha.com/input?i=plot+y%3D255*%28x%2F255%29%5E0.25+from+0+to+255
#define NONLINEARIZATION_EXPONENT 0.25



/**********************************************************
  KOODI ALKAIS SIT TÄSTÄ
**********************************************************/ 
#include <math.h>

// ********
// filtterit
// ********

// Tämä taulukko hilloaa INPUT_FILTER_N kpl edellistä sensorin raaka-arvoa.
unsigned int inputBuffer[INPUT_FILTER_N];

// Tälle annetaan aina uusi "raaka-arvo", ja se pullauttaa ulos suodatetun arvon.
// suodatetun arvon perusteella voi sitten katsoa tarvitaanko jarrua vai ei, ja kuinka paljon.
// Tyypiltään tämä on eksponentiaalinen liukuva keskiarvo, eli se painottaa tuoreita arvoja enemmän kuin vanhoja arvoja.
unsigned int getFilteredInputValue(unsigned int value) {

	// siirrä arvoja yksi pykälä eteenpäin
	for(int i=INPUT_FILTER_N-1; i>0; i--) {
		inputBuffer[i] = inputBuffer[i-1];
	}
	// ja laita uusin arvo indeksiin 0
	inputBuffer[0] = value;
	
	// ja filtteröi. Tässä siis lasketaan tietyllä tavalla painotettu summa puskurin arvoista
	// Tämä painottaa tuoreita arvoja enemmän kun vanhoja. 
	float filteredValue = inputBuffer[0];
	for (int i=INPUT_FILTER_N; i>0; i--) {
		filteredValue = (INPUT_FILTER_ALPHA * inputBuffer[i]) + ((1.0 - INPUT_FILTER_ALPHA) * filteredValue);
	}

	// palautetaan se kokonaislukuna
	return (unsigned int) filteredValue;
}


// Tämä taulukko hilloaa OUTPUT_FILTER_N kpl edellistä sensorin raaka-arvoa.
unsigned int outputBuffer[OUTPUT_FILTER_N];

// Tälle annetaan aina uusi "raaka-arvo", ja se pullauttaa ulos suodatetun arvon.
// Tyypiltään tämä on liukuva keskiarvo
unsigned int getFilteredOutputValue(unsigned int value) {

	// siirrä arvoja yksi pykälä eteenpäin
	for(int i=OUTPUT_FILTER_N-1; i>0; i--) outputBuffer[i] = outputBuffer[i-1];

	// ja laita uusin arvo indeksiin 0
	outputBuffer[0] = value;
	
	// ja filtteröi
	float filteredValue = 0;
	for (int i=0; i<OUTPUT_FILTER_N; i++) filteredValue = outputBuffer[i] + filteredValue;
	filteredValue = filteredValue/OUTPUT_FILTER_N;

	// palautetaan se kokonaislukuna
	return (unsigned int) filteredValue;
}



// Potenssifunktioskaalaus, eli tämä funktio tekee epälinearisoinnin
// yhtälö:  result = 255 * (input/255)^eksponentti
int powerScaling(int input) {
    double result;
    
    result = 255 * pow((double) input / 255, NONLINEARIZATION_EXPONENT);

    // Rajoita tulos välille 0-255
    if (result < 0) result = 0;
    if (result > 255) result = 255;

    return (int) result;
}




// ********
// pulssilaskuri
// ********

volatile unsigned long previousSensorInputMillis = 0;


volatile unsigned int pulseCount;
void pulseCounter() {
	int counter = 0;

	unsigned long currentMillis = millis();

	// Keskeytyksen lyödessä tarkistetaan pinnin tila vielä kolmesti.
	for(int i=0; i<INPUT_PULSE_RECHECKS; i++) {
		if(!digitalRead(SENSOR_INPUT_PIN)) counter++;
	}
	// Kaikkien kolmen pitää olla samat, muuten kyseessä kohina, mistä ei välitetä.
	if (counter >= INPUT_PULSE_RECHECK_MIN) {
		// Edellisestä pulssista pitää olla kulunut vähintään NNN millisekuntia,. 
		if(currentMillis >= (previousSensorInputMillis + INPUT_PULSE_HOLDOFF)) {
			pulseCount++;
		}
		previousSensorInputMillis = currentMillis;
	}

	// tää vähän auttaa sen anturin asemoinnissa.
	#if defined(SENSORLED)
		digitalWrite(LED_PIN, !digitalRead(LED_PIN));
	#endif
}




// ********
// päälogiikka
// ********
unsigned long previousMillis = 0;
void loop() {
	unsigned int value, rawValue, rawPwmValue, pwmValue, pwmValueToSet;
	unsigned long currentMillis = millis();

	if (currentMillis - previousMillis >= LOOP_INTERVAL) {
		previousMillis = currentMillis;
		
		// nollataan watchdog-ajastin
		rp2040.wdt_reset();
		
		// haetaan pulssien määrä
		rawValue = pulseCount;
		pulseCount = 0;
		
		// skaalataan saatu pulssimäärä taajuudeksi
		rawValue = rawValue * (1000/LOOP_INTERVAL);
		
		// tarviiko filtteröidä?
		#if defined(USE_INPUT_FILTER)
			value = getFilteredInputValue(rawValue);
		#else
			value = rawValue;
		#endif
		
		// funtsitaan jarrun asento.
		pwmValue = 0; // oletuksena jarru pois
		rawPwmValue = 0; // oletuksena jarru pois
		if(value > BRAKE_LEVEL_MIN) {
			// tarvitaan jarrua, mutta kuinka paljon?
			if(value > BRAKE_LEVEL_MAX) {
				// täys jarru+
				rawPwmValue = PWM_MAX;
			} else {
				// sopiva jarru
				rawPwmValue = PWM_MAX * 1.0 / (BRAKE_LEVEL_MAX - BRAKE_LEVEL_MIN) * (value - BRAKE_LEVEL_MIN);
			}
		}		

		// tarviiko filtteröidä?
		#if defined(USE_OUTPUT_FILTER)
			pwmValue = getFilteredOutputValue(rawPwmValue);
		#else
			pwmValue = rawPwmValue;
		#endif


		// Tarviiko se PWM:n arvo vielä epälinearisoida?
		#if NONLINEARIZATION_FUNCTION == POWER
			pwmValueToSet = powerScaling(pwmValue);
		#else
			pwmValueToSet = pwmValue;
		#endif


		// asetetaan se PWM.
		analogWrite(PWM_OUTPUT_PIN, pwmValueToSet);


		#if defined(SERIALDEBUG)
			Serial.print("input value: ");
			Serial.print(rawValue);
			Serial.print("\t filtered: ");
			Serial.print(value);
			Serial.print("\t raw PWM: ");
			Serial.print(rawPwmValue);
			Serial.print("\t filtered PWM Setting: ");
			Serial.print(pwmValue);
			Serial.print("\t nonlinearized PWM Setting: ");
			Serial.println(pwmValueToSet);
		#endif
	}
}






// ********
// alustukset
// ********

void setup() {
	#if defined(SENSORLED)
		pinMode(LED_PIN, OUTPUT);
	#endif

	// Watchdog boottaa tän, jos käy hassusti.
	rp2040.wdt_begin(LOOP_INTERVAL*3);

	// Nollaillaan filtterin puskurit, jos tarvii.
	#if defined(useInputFilter)
		for(int i=0; i<INPUT_FILTER_N; i++) inputBuffer[i] = 0;
	#endif
	#if defined(useOutputFilter)
		for(int i=0; i<OUTPUT_FILTER_N; i++) outputBuffer[i] = 0;
	#endif

	// nollataan pulssilaskuri
	pulseCount = 0;

	// PWM lähtö
	pinMode(PWM_OUTPUT_PIN, OUTPUT);
	analogWriteFreq(PWM_FREQUENCY);
	analogWriteRange(255);
	analogWriteResolution(8);
	analogWrite(PWM_OUTPUT_PIN, 0);
	
	// Tää on testimoodi jarruvoiman testaukseen. Ei tuotantokäyttöön
	#if defined(TESTMODE_BRAKELEVEL)
		analogWrite(PWM_OUTPUT_PIN, TESTMODE_BRAKELEVEL);
		while(1) {
			digitalWrite(LED_PIN, !digitalRead(LED_PIN));
			delay(50);
			rp2040.wdt_reset();
		}
	#endif

	// Tää on testimoodi, joka replikoi sen anturin tilanteen. Ei tuotantoon
	// Huom. Tässä ei ole mitään kohinasuodinta mukana!
	#if defined(TESTMODE_LEDBLINKER)
		pinMode(SENSOR_INPUT_PIN, INPUT_PULLUP);
		while(1) {
			digitalWrite(LED_PIN, !digitalRead(SENSOR_INPUT_PIN));
			rp2040.wdt_reset();
		}
	#endif

	// Tähän tulee nopeusanturin pulssit
	pinMode(SENSOR_INPUT_PIN, INPUT_PULLUP);
	attachInterrupt(digitalPinToInterrupt(SENSOR_INPUT_PIN), pulseCounter, FALLING);

	// debuggi-tuloste sarjaporttiin, jos sellaista käytetään
	#if defined(SERIALDEBUG)
		Serial.begin(115200);
	#endif

	// nollataan vielä watchdog-ajastin
	rp2040.wdt_reset();
}

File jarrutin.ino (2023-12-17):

/* 
	Jarru
	
	Yritetty kirjoittaa niin, että on luettavissa ja ymmärrettävissä.
	Ei siis mitään turhan hienoja juttuja tai mitään kirjastoja.

	Arduino IDE: 2.2.1
	Board manager url: https://github.com/earlephilhower/arduino-pico/releases/download/global/package_rp2040_index.json
  Board: Raspberry Pi Pico
	´

changelog

	ver 0.1:
		Eka proto Arduinolla (joku ATMEGA)
		Periaate todettiin toimivaksi
		
	ver 0.2:
		Porttaus Raspberry Pi Picolle
		Kommentoitu
		Parametrit nätisti
		Lisätty suodin vähän pehmentämään jarrutuksen muuttumista
*/

// jos tämä on määritelty, tulosteleee USB-uarttiin miten menee.
// tuotantoversiota varten kommentoi pois.
#define SERIALDEBUG

// brakeMinLevel kertoo millä nopeudella (pulssia/sekunti) jarrutus alkaa
#define brakeMinLevel 50

// brakeMaxLevel kertoo millä nopeudella (pulssia/sekunti) jarrutus on TÄYSILLÄ
#define brakeMaxLevel 400

// loopInterval (ms) kertoo kuinka usein tila päivitty. 125 ms, eli 8hz lienee aika sopiva
#define loopInterval 125

// nää määrittelis minne PWM ja sensori olis kytketty.
#define pwmOutputPin 5
#define sensorInputPin 13

// tämä kertoo käytetäänkö pehmentämiseen filtteriä vai ei. Kommentoi pois, jos ei.
#define useInputFilter
// Filtteri on eksponentiaalinen liukuva keskiarvo, eli viimeisintä arvoa painotetaan eniten ja vanhinta vähiten
// inputFilterN kertoo suotimen pisteiden määrän.  125 ms loopIntervallilla n=16 tarkoittaa kahta sekuntia
#define inputFilterN 12
// inputFilterAlpha on ulostulon suotimen painotusten "jyrkkyys".
#define inputFilterAlpha 0.2

// pwmFrequency kertoo millä taajuudella fettiä ajetaan. korkeampi taajuus vie vinkumisen korkeille taajuuksille (eikä kuulu, mutta fetti voi lämmetä enemmän)
#define pwmFrequency 8000

// pwmMax kertoo pwm-jarrun suurimman arvon. Sinne pitää jättää vähän löysää, että prossu pysyy virroissa. 255 arvo johtaa prossun boottaamiseen.
// arvolla 250 noin 2% moottorin tuottamasta energiasta on jarruohjaimen käytettävissä. Sen pitäis riittää.
#define pwmMax 250




/**********************************************************
  KOODI ALKAIS SIT TÄSTÄ
**********************************************************/ 

// ********
// filtteri
// ********

// Tämä taulukko hilloaa inputFilterN kpl edellistä sensorin raaka-arvoa.
unsigned int inputBuffer[inputFilterN];

// Tälle annetaan aina uusi "raaka-arvo", ja se pullauttaa ulos suodatetun arvon.
// suodatetun arvon perusteella voi sitten katsoa tarvitaanko jarrua vai ei, ja kuinka paljon.
// Tyypiltään tämä on eksponentiaalinen liukuva keskiarvo, eli se painottaa tuoreita arvoja enemmän kuin vanhoja arvoja.
unsigned int getFilteredInputValue(unsigned int value) {

	// siirrä arvoja yksi pykälä eteenpäin
	for(int i=inputFilterN-1; i>0; i--) {
		inputBuffer[i] = inputBuffer[i-1];
	}
	// ja laita uusin arvo indeksiin 0
	inputBuffer[0] = value;
	
	// ja filtteröi
	float filteredValue = inputBuffer[0];
  for (int i=0; i<inputFilterN; i++) {
      filteredValue = (inputFilterAlpha * inputBuffer[i]) + ((1.0 - inputFilterAlpha) * filteredValue);
  }

	// palautetaan se kokonaislukuna
	return (unsigned int) filteredValue;
}



// ********
// pulssilaskuri
// ********

volatile unsigned int pulseCount;
void pulseCounter() {
	// tää vain laskee saapuneita keskeytyksiä 
	pulseCount++;
}



// ********
// päälogiikka
// ********
unsigned long previousMillis = 0;
void loop() {
	unsigned int value, rawValue, pwmValue;
	
		unsigned long currentMillis = millis();
	if (currentMillis - previousMillis >= loopInterval) {
		previousMillis = currentMillis;
		
		// nollataan watchdog-ajastin
		rp2040.wdt_reset();
		
		// haetaan pulssien määrä
		rawValue = pulseCount;
		pulseCount = 0;
		
		// skaalataan saatu pulssimäärä taajuudeksi
		rawValue = rawValue * (1000/loopInterval);
		
		// tarviiko filtteröidä?
		#if defined(useInputFilter)
			value = getFilteredInputValue(rawValue);
		#else
			value = rawValue;
		#endif
		
		// funtsitaan jarrun asento.
		pwmValue = 0; // oletuksena jarru pois
		if(value > brakeMinLevel) {
			// tarvitaan jarrua, mutta kuinka paljon?
			if(value > brakeMaxLevel) {
				// täys jarru+
				pwmValue = pwmMax;
			} else {
				// sopiva jarru
				pwmValue = pwmMax * 1.0 / (brakeMaxLevel - brakeMinLevel) * (value - brakeMinLevel);
			}
		}		

		// asetetaan se PWM.
		analogWrite(pwmOutputPin, pwmValue);

		#if defined(SERIALDEBUG)
			Serial.print("raw value: ");
			Serial.print(rawValue);
			Serial.print("\t filtered value: ");
			Serial.print(value);
			Serial.print("\t PWM Setting: ");
			Serial.println(pwmValue);
		#endif
	}
}




// ********
// alustukset
// ********

void setup() {
	// Watchdog boottaa tän, jos käy hassusti.
	rp2040.wdt_begin(loopInterval*3);

	// Nollaillaan filtterin puskuri, jos tarvii.
	#if defined(useInputFilter)
		for(int i=0; i<inputFilterN; i++) inputBuffer[i] = 0;
	#endif

	// nollataan pulssilaskuri
	pulseCount = 0;

	// Tähän tulee nopeusanturin pulssit
	pinMode(sensorInputPin, INPUT);
	attachInterrupt(digitalPinToInterrupt(sensorInputPin), pulseCounter, RISING);

	// PWM lähtö
	pinMode(pwmOutputPin, OUTPUT);
	analogWriteFreq(pwmFrequency);
	analogWriteRange(255);
	analogWriteResolution(8);
	analogWrite(pwmOutputPin, 0);
	
	// debuggi-tuloste sarjaporttiin.
	#if defined(SERIALDEBUG)
		Serial.begin(115200);
	#endif

	// nollataan vielä watchdog-ajastin
	rp2040.wdt_reset();
}

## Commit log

2024-01-13 Added hardware documentation
    [Pico.skp, Test.kicad_pcb, Test.kicad_sch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]
2024-01-15 Adds BOM and updates HW design
    [jarrutin.kicad_sch, jarrutin_BOM.csv, jarrutin_BOM.xlsx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]
2024-01-17 Updated schematic
    [jarrutin.kicad_sch]
2024-01-19 Update based on final implementation
    Updated design, based on tests done 19.01.24. Functionality of hardware and software has been proven and the remaining issue is getting rid of dissipated power from diodes and FETs.
    [jarrutin.kicad_sch]
